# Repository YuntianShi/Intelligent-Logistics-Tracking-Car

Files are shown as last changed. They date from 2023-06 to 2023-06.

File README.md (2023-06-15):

# Intelligent-Logistics-Tracking-Car
This is a course design from Design &amp; Bulid Ⅰ(First Semester) and I am the leader of this project.  

<p align="center">
摘要
</p>  

&emsp;&emsp;智能机器人从诞生至今已经有了长足进步和发展。其中，能够自由移动对外界环境作出反应的智能循迹机器人更是其中的佼佼者，早已是智能机器人研究的重点领域。智能循迹机器人随着机械领域、计算机领域、微电子领域、自动化领域、传感领域等相关领域技术的不断发展突破而日俞完善，并逐渐广泛的应用于工业操作、宇宙探测、疫情管控、科研、军事和民用等方面。  

&emsp;&emsp;近年来，各大高校纷纷面向本科生开展智能机器人制作课程，立足于激发大学生的创新意识，培养学生的动手和团队协作能力。我校为培养新工科人才，为学生奠定良好的基础，设立了制作基于Arduino开发板的“智能派送车”项目。本文以“智能派送车”为研发对象，研究并设计了一种“塔”式投放的智能派送车，并进行了相应的商业可行性分析。  

&emsp;&emsp;首先，本项目研究了项目开发相应流程，确定了项目开发的日历和甘特图，对工作进行初步分解，进行组内团队分工，做出项目产品规划，确定了产品规格并进行了客户需求调研。  

&emsp;&emsp;其次，本文对研发对象进行了功能分解，确定产品整车结构-“塔”式结构，建立三维模型，绘制产品工程图，进行动画仿真，确定控制接线图，确定控制逻辑判断流程并写出相应代码。  

&emsp;&emsp;再次，确定零件毛胚规格，制作关键零件，购买外购件，经济预算控制，并完成整车组装、综合调试和优化相关工作。  

&emsp;&emsp;最后，在完成“智能派送车”制作的基础上，我们进行了项目开发经济分析、项目产品开发对社会的影响，确保了商业上的经济可行性。  

&emsp;&emsp;总之，本项目从现实入手，关注在全球疫情下的行业问题，结合商业经济分析，通过对机械、计算机、微电子、传感、自动化领域知识的运用，将创意转换为产品，在一组成员的共同努力之下，顺利完成了课程任务。  

&emsp;&emsp;接下来是一些项目图片展示：  

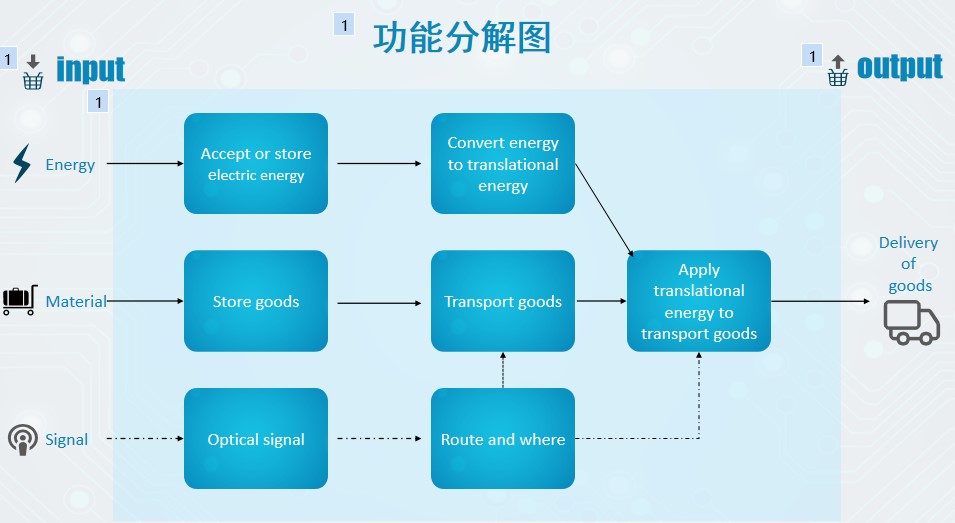
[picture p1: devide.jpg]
   

<p align="center">
图1 产品目标树
</p>  

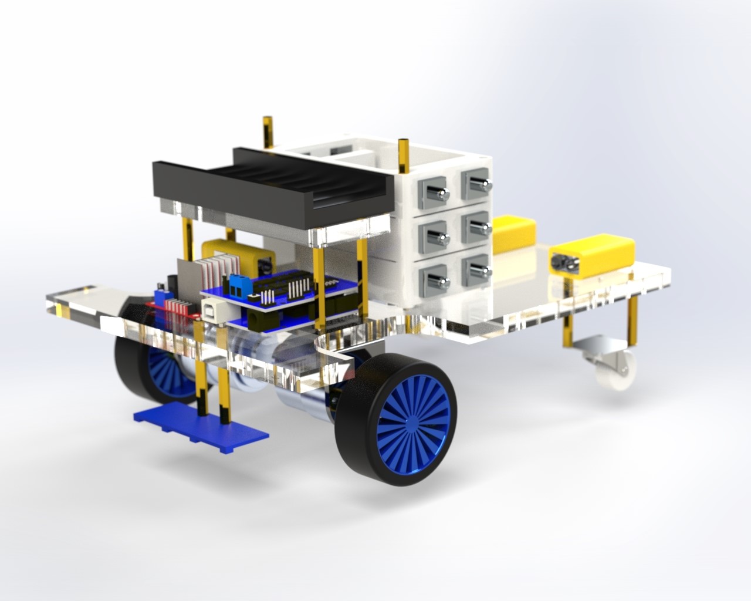
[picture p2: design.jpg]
  

<p align="center">
图2 整车设计图
</p>  

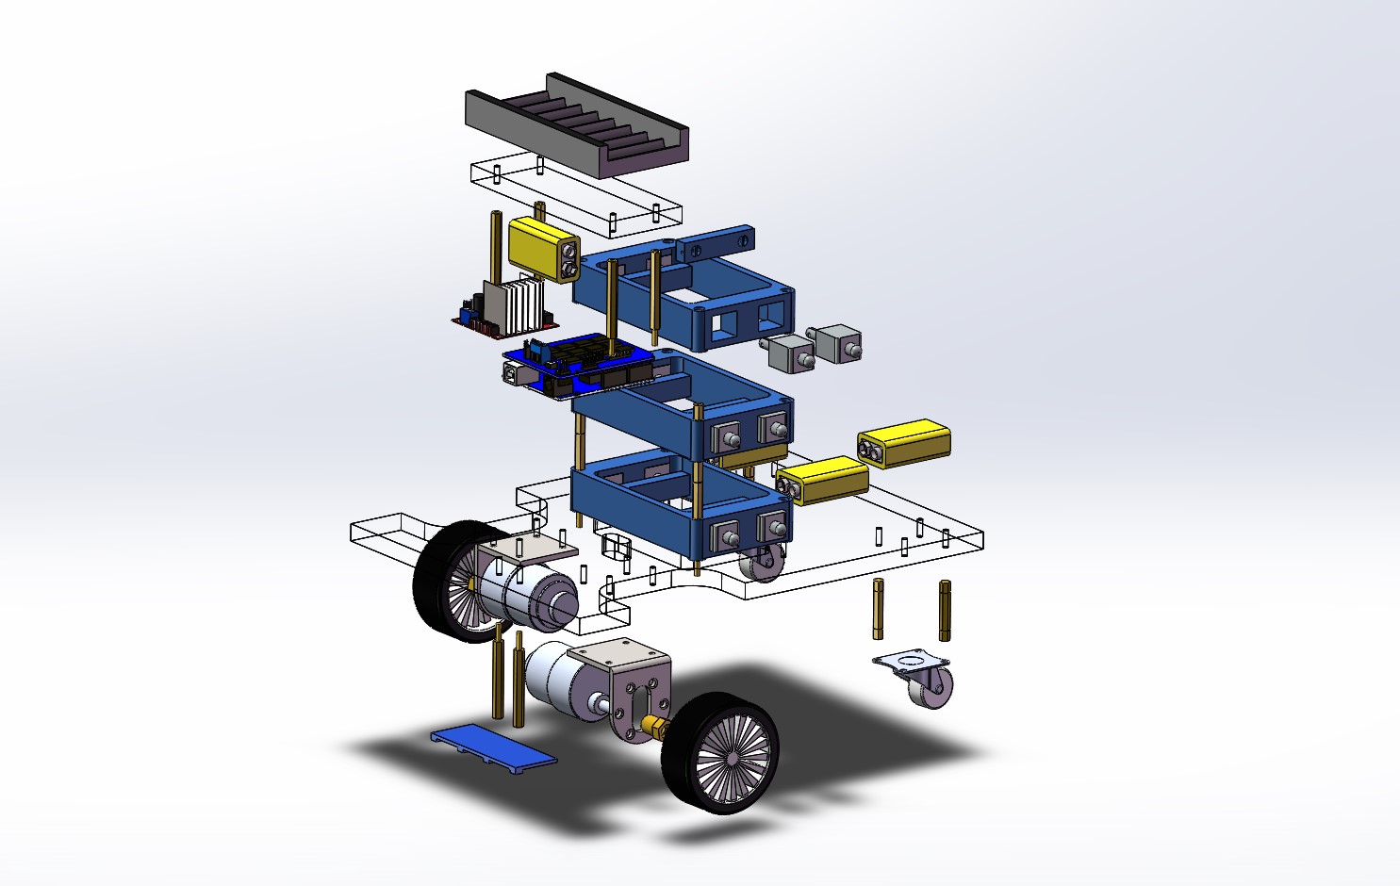
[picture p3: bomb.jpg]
   

<p align="center">
图3 整车爆炸图
</p>  

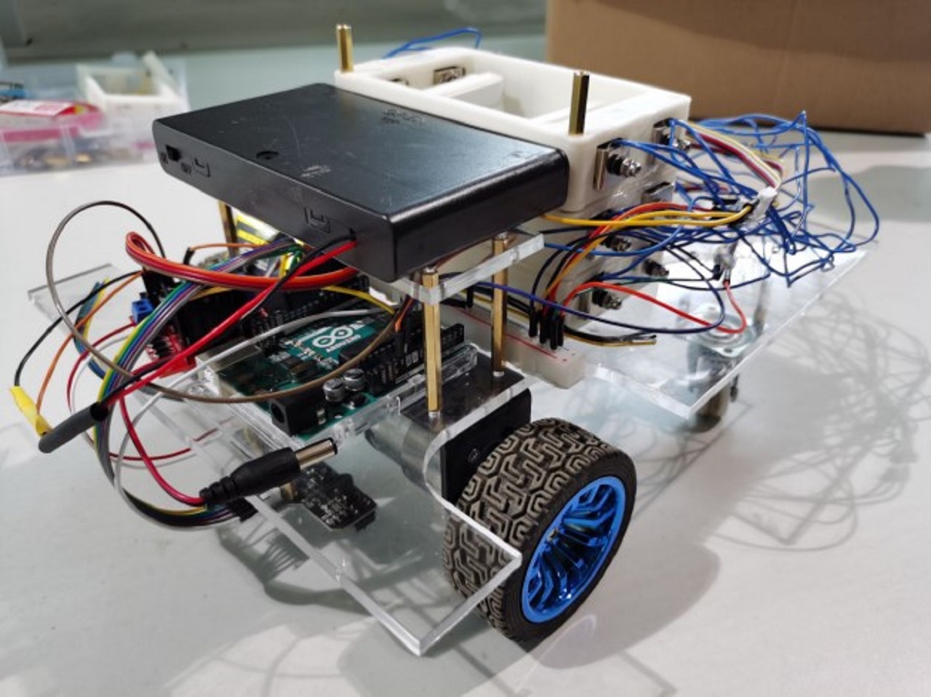
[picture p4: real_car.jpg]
  

<p align="center">
图4 实物演示图
</p>  

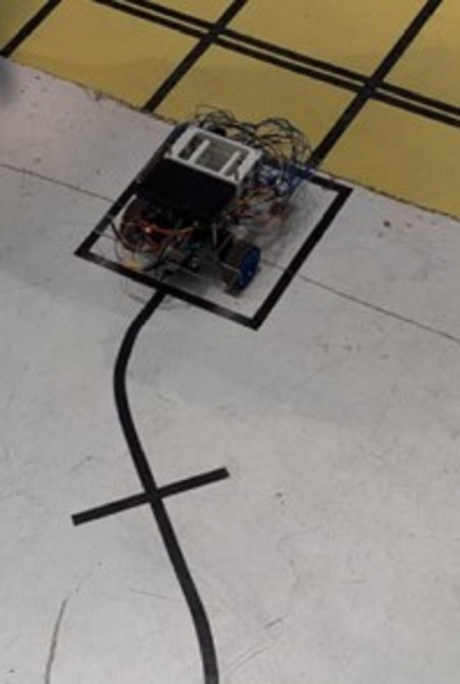
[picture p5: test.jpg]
   

<p align="center">
图5 实物测试图
</p>

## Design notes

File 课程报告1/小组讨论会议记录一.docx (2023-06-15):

设计与建造 课程小组会议记录

议题 | | 课程报告一
组长 | | 袁萌启 | 年级/班级/组别 | | | 2020级 2 班 第 1 组
组员 | | 石云天，马天翼，季若鱼，李贺航
会议时间 | 2020年9月30日 | | | 会议地点 | 46教A114
讨论内容 | 1.智能派送车的项目综述 2.团队组成分工与工作分解 3.团队接下来的计划以及团队日历和甘特图 4.工程师职责 5.对给课程所需知识进行初步的认识
下一步工作计划 | 进行产品规划，完成产品任务书以及产品任务调研，对客户需求进行分析，完成产品目标树，确定产品目标指标，产品规格参数，建立需求-指标矩阵。 对组内成员进行进一步了解，对组内分工进行调整和细化。
附件材料清单 | 《产品的设计和开发》，《Arduino程序设计基础》 《机械工程图学》

参会成员签字:袁萌启、马天翼、石云天、季若鱼、李贺航

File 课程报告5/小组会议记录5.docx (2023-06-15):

设计与建造 课程小组会议记录

议题 | | 课程报告五
组长 | | 袁萌启 | 年级/班级/组别 | | | 2020级 2 班 第 1 组
组员 | | 石云天，季若鱼，李贺航，马天翼
会议时间 | 2020.11.29 | | | 会议地点 | 郑东图书馆206读者研究厢
讨论内容 | 1. 对老师上课内容进行梳理。 2.对本次小组任务进行具体的分工。 3.整车装配并生成爆炸拆解，完成投放动画仿真。 4.设计控制系统并完成连线图。 5.绘制控制流程图并设计算法，完成代码。
下一步工作计划 | 1. 购置零件毛坯材料并确定尺寸规格。 2. 进行关键零件的制作并准备项目产品装配。 3. 准备实地测验并进行后期调试。
附件材料清单 | 《产品的设计和开发》 《Arduino程序设计基础》

参会成员签字：袁萌启，石云天，李贺航，马天翼，季若鱼

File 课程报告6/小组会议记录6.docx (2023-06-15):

设计与建造 课程小组会议记录

议题 | | 课程报告六
组长 | | 袁萌启 | 年级/班级/组别 | | | 2020级 2 班 第 1 组
组员 | | 石云天，季若鱼，李贺航，马天翼
会议时间 | 2020.12.10 | | | 会议地点 | 郑东图书馆206读者研究厢
讨论内容 | 1. 对老师上课内容进行梳理。 2.对本次小组任务进行具体的分工。 3.购置零件毛坯材料并确定尺寸规格。 4.进行关键零件的制作并准备项目产品装配。 5.准备实地测验并进行后期调试。
下一步工作计划 | 1. 对产品开发过程进行经济性分析，对成本进行把握。 2. 分析项目产品开发对社会的影响，做进一步的思考与准备。 3. 完成项目产品报告书，准备进行答辩。
附件材料清单 | 《产品的设计和开发》 《Arduino程序设计基础》

参会成员签字：袁萌启，石云天，李贺航，马天翼，季若鱼

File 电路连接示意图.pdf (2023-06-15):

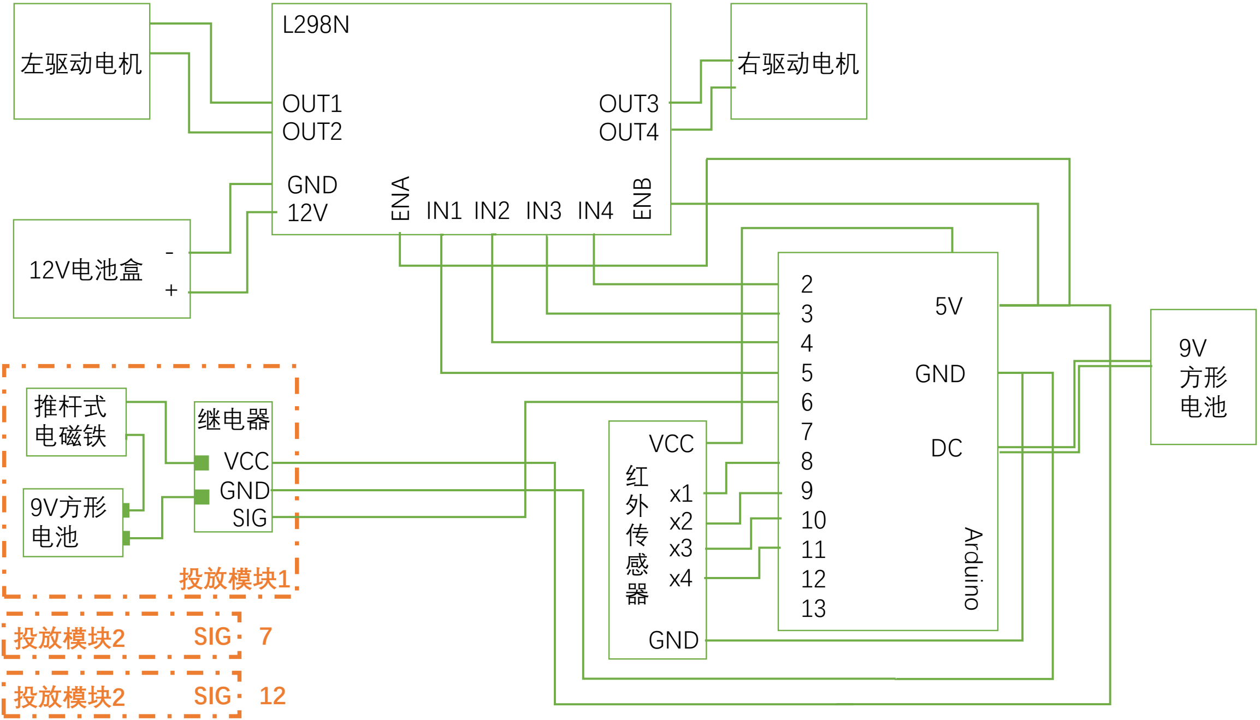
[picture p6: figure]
OUT1 OUT2; OUT3 OUT4; ENA; ENB; GND; 左驱动电机; 右驱动电机; 12V电池盒; 红外传感器; VCC; Arduino; 电池 继电器; VCC GND SIG 9V方形 电池; 推杆式 电磁铁; 投放模块; 2 SIG; SIG

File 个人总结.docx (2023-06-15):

石云天个人总结

进入大学的第一个学期，我接触到了一种以前从未接触过的教学方式——项目制教学，也第一次以小组的形式完成一整门课程。一个学期的时间眨眼间就过去了，设计与建造课程也要到了结课的时候，回顾这一个学期的课程，虽然十分辛苦，但在巨大的收获与最后成功带来的喜悦幸福面前，又显得不值一提。

首先，我想感谢为了这门课默默付出的每位老师、学长以及我最靠谱的队友们，没有每位老师的辛苦付出与耐心解答，我就没有机会体验到产品设计生产的整个工艺流程，没有机会收获这么多实用的知识与宝贵的实践机会。我的队友一直是我背后最坚实的后盾，我们在遇到困难时相互鼓励，在知识上互相交流、学习进步。这种相互促进、共同进步的氛围让我感到十分可贵，希望在日后其他的课程中也可以拥有这样的良师益友。

其次，我来陈述一下我在这个项目中为团队做出的贡献：制作课程报告一到六，完成报告书主体内容撰写，全程参与小车装配与程序调试；在整个学期的学习和探讨过程中：根据课程安排制作团队日历与项目安排甘特图；查阅并学习机电控制有关知识；根据客户需求调研结果完成产品目标树；学习并向组内同学讲述产品规划五步骤，协助完成产品任务书；学习并向组内同学讲述产品概念生成五步法，完成形态矩阵表与产品概念组合；完成驱动概念评分矩阵表；手绘小车草图；参与转向机构设计；建立项目产品三维模型；绘制项目产品2D图；绘制控制策略的逻辑判断流程图；制作投放机构投放动画仿真；参与代码编写；参加关键零件制作；参与整车装配与调试；确定零件毛坯材料与规格；学习相关知识并完成敏感性分析，绘制相关表格；完成小组会议记录七。通过这些任务的历练，我收获了许多。

最后，也是最重要的一个部分，我想说一下我的收获。

1、了解了整个设计生产的工艺流程。这门课设立的初衷就是让我们与实际的生产生活接轨，让我们了解现在实际生产中会应用哪些技术、使用哪些方法、在未来的实际工作中会面临怎样的情况，这也是天津大学“新工科”培养理念的最好体现。这门课从项目管理、产品规划、概念设计、详细设计、机电控制、代码调试、经济分析等多个方面由专业的老师系统地向我们介绍了相关的知识，然后以自己的智能投放小车作为实例，加以实践和运用。活学活用让我们的认识更加深刻、理解更加透彻。

2、极大的锻炼了我的沟通表达能力与团队协作能力。这门课创造性的开设了研讨课的形式，要求我们能够把自己的想法清楚明白的表达给别人，同时要符合任务规定的要求。我从最开始的不适应、不知所措到后来逐渐熟练、得心应手，是这门课的不断练习让我的表达能力得到提升，心理素质取得进步。这门课以小组方式进行，团队合作能力也是十分关键的，由于彼此之间不够熟悉，各自性格也不够了解，最开始的几次合作都陷入了僵局。但好在有组长的组织，他帮助我们破冰，化解尴尬气氛，经过几次的磨合，团队终于走上了正轨。我一直在反思之前我的问题，我有些过于内向，经常闷着不与同学交流，导致合作无法推进。从这之后，在每次小组会议上我都有意的增加我的发言，让队友可以及时了解我的意见与看法，最后的效果得到了明显的改进。这一学期的合作让我明白跟别人合作一定要足够主动，不要只是被动的听和接受，这样才能提高合作的效率，我相信这些收获在日后的学习和生活中一定会让我受益匪浅。

3、学会了很多软件的应用，激发了自学的热情与动力。设计与建造这门课有许多知识是需要我们在课下自学完成的，还有很多操作的实际演练是需要在课后完成的。这其中最有代表性的就是SOLIDWORKS的应用，最开始的时候只听了老师的讲解，课后自己操作时，只是一个小小的零件却花了我三个小时，当时我十分失望，甚至对自己的能力产生了怀疑。但正所谓“熟能生巧”，在队友的鼓励下，经过不断反复的练习，我可以比较熟练的操作了，真正掌握之后，我对这个软件产生了浓厚的兴趣，在课余时间会自己制作其他东西的3D模型，遇到不会的操作就去百度、去书上寻找解决的办法，在实践中探索学习，越学越有兴趣，既收获了技术，又收获了做完的快乐与成就感。通过这门课程我还掌握了arduino编程语言、fritzing软件绘制电路连线图、一部分机电控制的知识，在实践中探索，找到学习的兴趣与动力。

4、磨练了追求卓越、不轻言放弃的精神与魄力。整个过程中，耗时最久、最困难的部分就是最后的实地调试与代码优化。我们的小车最开始只能以三十多秒跑完整个赛道，并且投放也没有那么的精准。但正是我们对高品质的追求，驱使着我们不断改进，然而绝大多数的调整与测试都是以失败而告终的，我们的情绪逐渐都陷入了低谷。但是前面的困难有多大，最后成功的喜悦也会有多么的鼓舞人心。功夫不负有心人，在无数次的优化、测试后，我们的小车终于以不到15秒的时间跑完了全程，并且投放也比以前精准了许多。这次的经历教会了我永远不要满足于现状，一定要追求卓越，争取更上一层楼。我坚信这也会是我一生最为宝贵的财富。

这短短的一个学期，有苦有甜，既有前期耕耘受挫的压抑，也有最后顺利完成的激动。我会带着心中的这份感激，以更好的自己面对未来更多未知的挑战。

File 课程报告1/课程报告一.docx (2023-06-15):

课程报告1 项目计划

1.1 项目相关资料综述

项目综述：1、项目任务相关：本项目壹团队为单位，设计、建造并运行智能派送车，课程结束时各团队携带设计成果参加竞赛，完成研制报告和答辩。派送车从出发区发车，跟随地面轨迹线自主驶向终点。途中完成三个包裹的投放任务。2、智能派送小车：由智能派送车代替人工快递，减轻人工工作负担，提高工作效率，同时减少疫情期间人员流动。

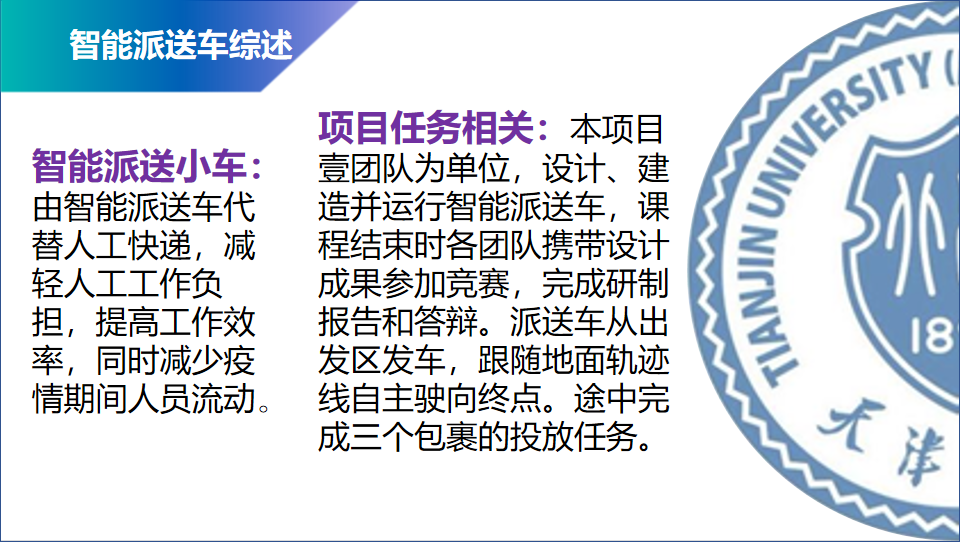
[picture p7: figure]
$[N360%(~$K[62R4L}Y)EOT

图1-1智能派送车综述

项目相关资料补充：1、工程：工程是利用科学原理来设计和建造机器，结构和其他项目，包括桥梁，隧道，道路，车辆和建筑物。工程学科包括广泛的更专业的工程领域；每个领域都更加侧重于应用数学，应用科学和应用类型的特定领域。2、工程设计：工程设计是一个系统化智能化的过程，在这个过程中，工程师为设备、系统或过程生成、评估和指定解决方案，这些设备、系统或过程的形式和功能在满足特定约束集的同时实现了客户的目标和用户的需求。换言之，工程设计是一个深思熟虑的过程，用于为设备、系统或过程生成计划或方案，这些设备、系统或过程在遵守特定约束的同时实现给定的目标。3、工程制图：工程图是生产中必不可少的技术文件，是在世界范围通用的“工程技术的语言”。正确规范的绘制和阅读工程图是一名工程技术人员必备的基本素质。制图的基本技能有尺规绘图、徒手绘图及计算机绘图。零件图、装配图的读图与绘制等。

4、机电一体化：机电一体化又称机械电子工程，是机械工程与自动化的一种，随着计算机技术的迅猛发展和广泛应用，机电一体化技术获得前所未有的发展。现在的机电一体化技术，是机械和微电子技术紧密集合的一门技术，他的发展使冷冰冰的机器有了人性化，智能化。5、机电一体化相关技术介绍：（1）精密机械技术(2)信息处理技术（3)检测与传感器技术（4)自动控制技术（5)伺服驱动技术（6）系统总体技术 6、Arduino: 构建于开放原始码simple I/O介面版，并且具有使用类似Java、C语言的Processing/Wiring开发环境。主要包含两个的部分：硬件部分是可以用来做电路连接的Arduino电路板；另外一个则是Arduino IDE，你的计算机中的程序开发环境。Arduino能通过各种各样的传感器来感知环境，通过控制灯光、马达和其他的装置来反馈、影响环境。板子上的微控制器可以通过Arduino的编程语言来编写程序，编译成二进制文件，烧录进微控制器。对Arduino的编程是通过 Arduino编程语言 (基于 Wiring)和Arduino开发环境(基于 Processing)来实现的。基于Arduino的项目，可以只包含Arduino，也可以包含Arduino和其他一些在PC上运行的软件，他们之间进行通信 (比如 Flash, Processing, MaxMSP)来实现。7、Arduino uno 简介：单片机： Arduino UNO控制器采用的是 Atmel 公司生产的ATmega328P-PU单片机。供电方式：1、USB接口通过USB 数据线,给UNO控制器提供5V的工作电压.2、通过5V引脚和GND供电,电压不大于5V。3、DC电源接口连接到UNO控制器上一个5V的稳压电路,给UNO控制器提供标准的5V工作电压。4、扩展引脚中的Vin引脚和DC电源接口一样。8、arduino平台特点：简单清晰、开放性、发展迅速。1.2 项目管理

团队组成：经过对有关知识的学习，我们了解了组成一个成熟的产品设计研发团队所需的分工大致如下：市场营销+设计（结构设计+电子设计）+制造+文案。同时结合我们小组成员的具体特长以及本着设计与建造课需要每位同学都学习到整个产品研发流程的宗旨，我们小组进行了如下的分工（每个人都会参与到整个智能小车设计开发的全过程，但分工有所侧重）：1、袁萌启：设置运输程序，设置循行路线，使小车能成功地完成任务，符合设计理念，达成初步设计，尽量满足市场调研所提出的市场需求。2、马天翼：主要负责快递小车的结构设计，需要规划快递装载与投放方案，设计小车行进方式，规划元器件布局，设计车体框架，使车体能构成完整系统，为任务提供硬件保障。3、石云天：负责利用机电一体化技术实现小车的运动停止，让小车有完整的驱动系统，同时利用arduino编程控制小车完成指定任务，实现智能化作业。4、季若鱼：负责完成课程报告书，ppt等文案的制作工作，并完成每位成员的任务完成情况小结以及小组的会议记录，和小组同学合作完成小车的制作。5、李贺航：对该方向智能机器人的发展历程进行调查，了解目前市场主流产品的优点及不足，确立该机器人研发过程中的方向。在后期产品制作的过程中负责对各零部件，主板等的绘图建模工作。

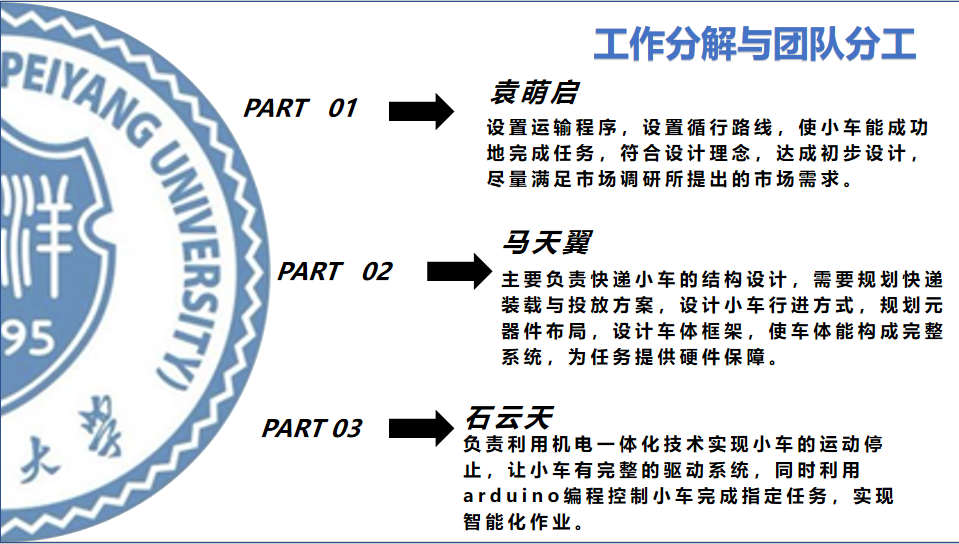
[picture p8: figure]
[VWECQA[2PA9Z1DA`LEHU)S
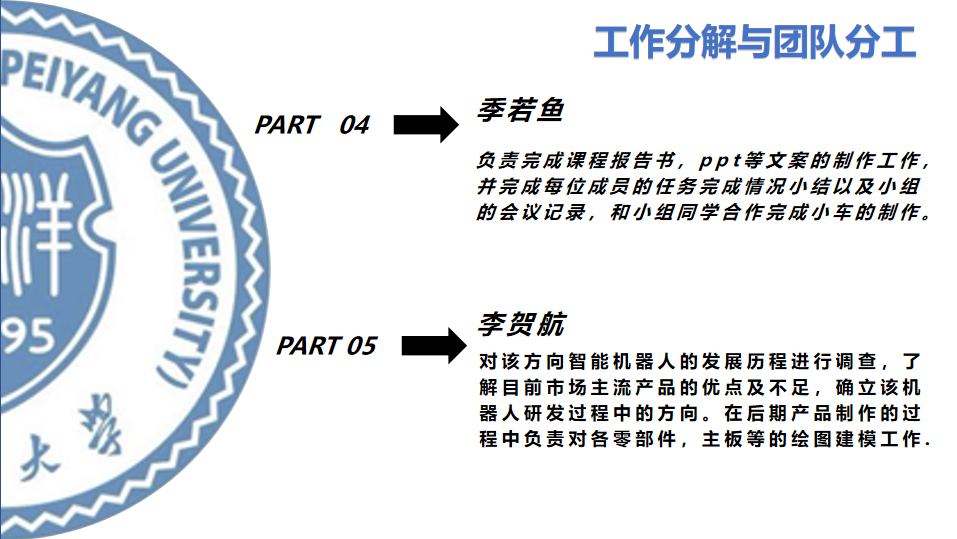
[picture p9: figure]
W{J(7H@X88TT$1}8Z5@2)G2

图1-2（a）团队组成与分工

图1-2（b）团队组成与分工

团队文化：有一个明确的挑战性的目标（智能配送车），从目标出发以结果构建团队结构，一群有才华有能力的团队成员，将团队需求放于个人需求之前的承诺，积极的团队文化（永不放弃，诚实守信，开创思维，相互尊重，民主开放），追求卓越的标准，从学部获得支持，团队有有效的领导。

工作分解：通过学习《产品的设计和开发》以及查阅产品研发的相关资料，我们小组把制造智能小车的项目进行了具体的工作分解，先是把它分成了八个子任务，而后又对子任务进行了更加细致的分解，利于我们以后更好的进行项目管理以及推动项目进展。

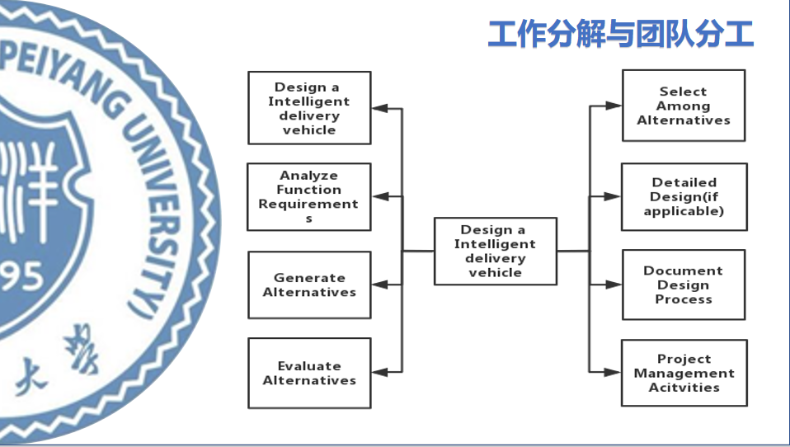
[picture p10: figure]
PR_UBB_3R%A}V}4[@(3(BZB
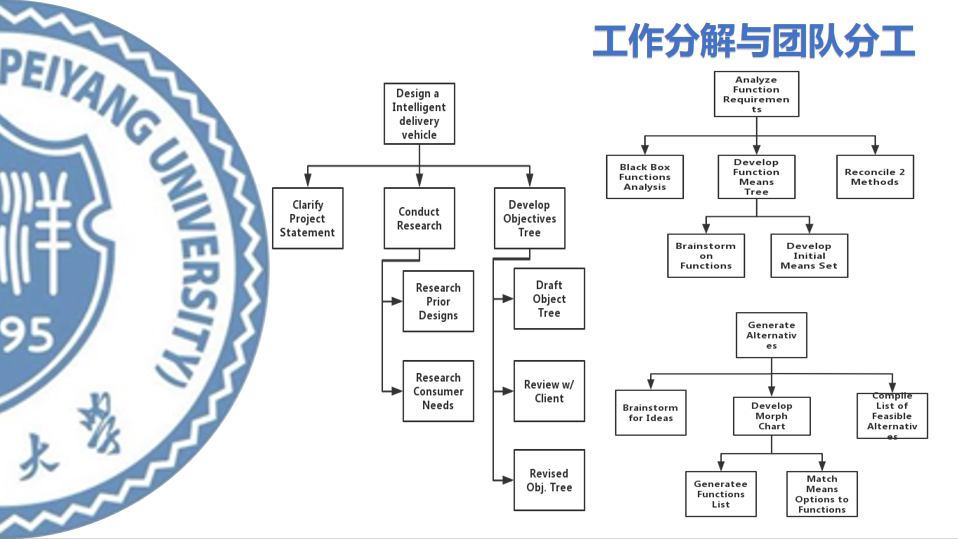
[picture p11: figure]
IGDXIKDPCQDB03Y5S)X9%EN

## 图1-2（c）工作分解

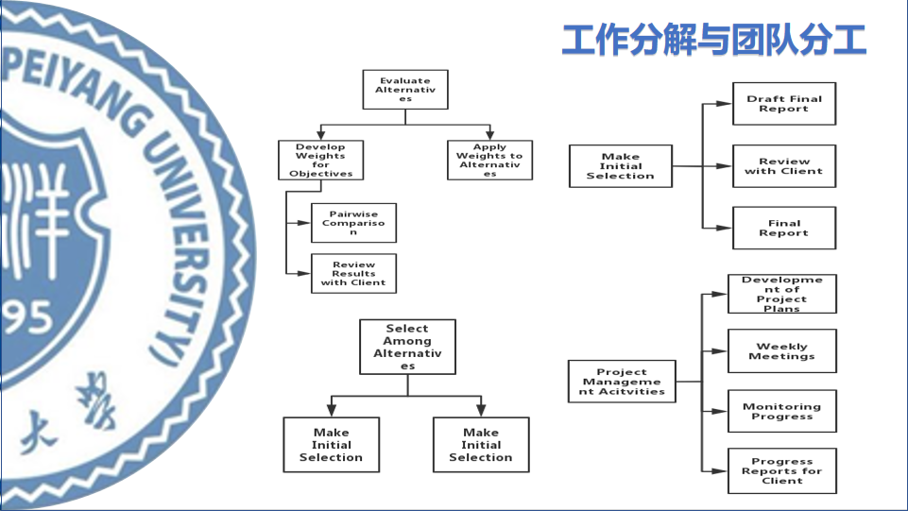
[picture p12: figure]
CK4FEP]}ZOXNFCRVPL(J4O0

## 图1-2（d）工作分解

图1-2（e）工作分解

团队日历：根据老师公布的课程安排以及自身的时间安排，我们制订出整个项目从开始阶段到最后成品制作完成的团队日历，让我们更加有计划的推动各个步骤的进展。

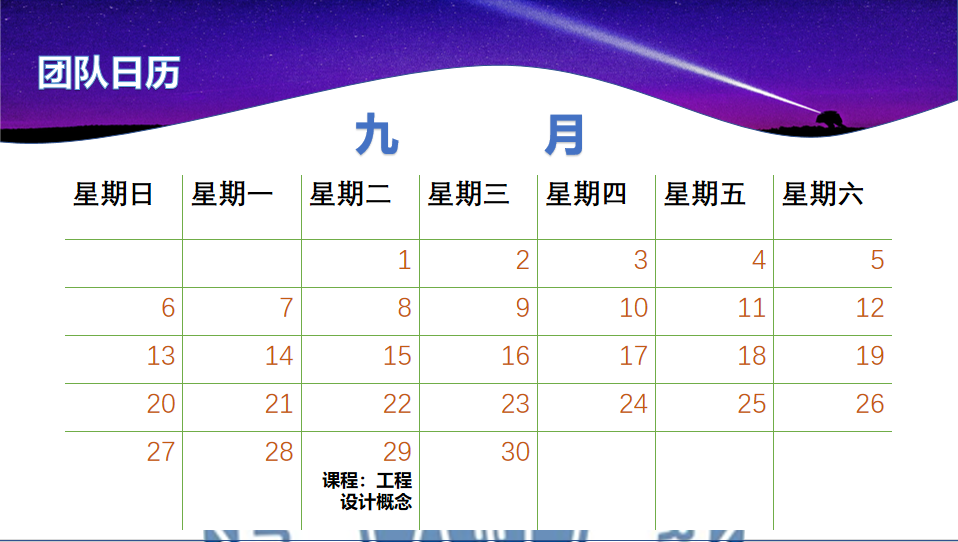
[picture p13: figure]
1]04S)S(92S3$]X]N0U{2ZV

图1-2（f）九月团队日历

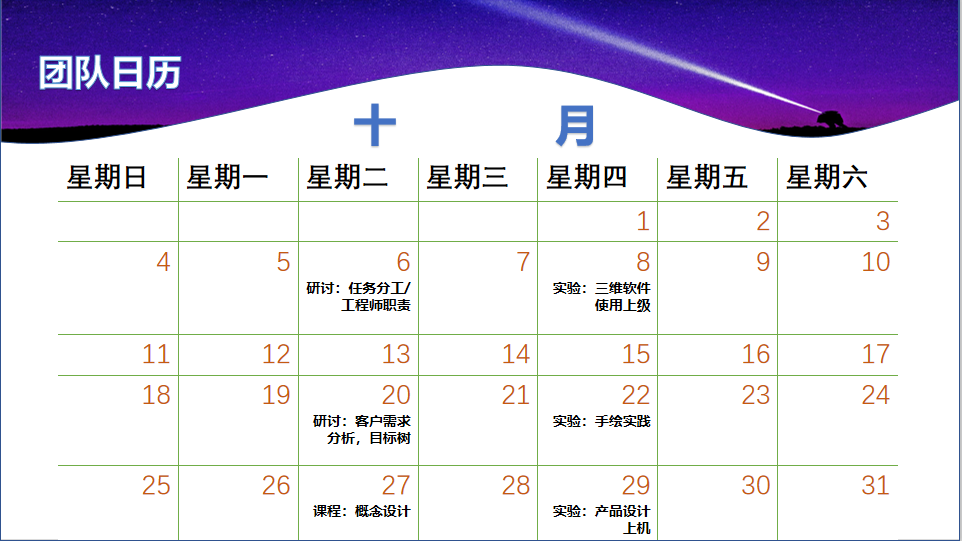
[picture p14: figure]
0`UL(A6_$}K$D)XN836]~{H
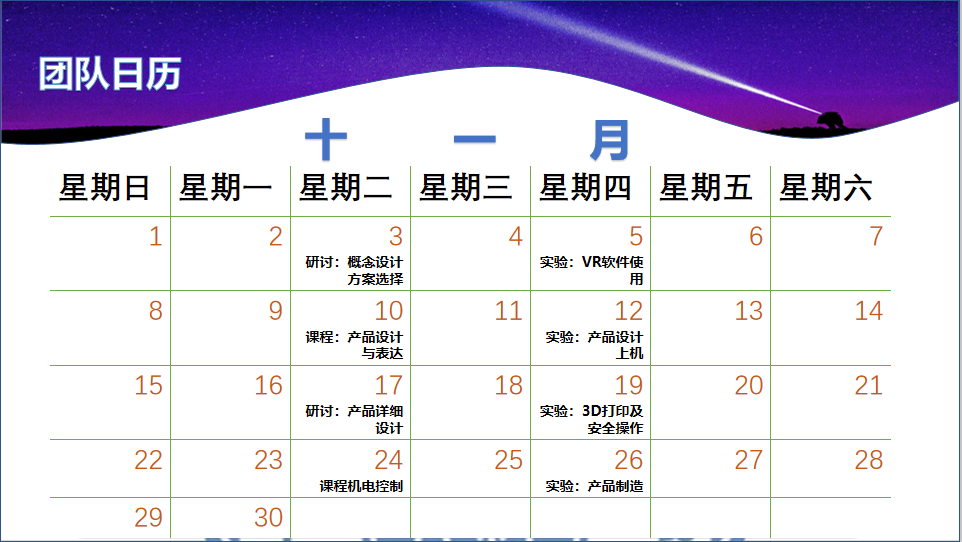
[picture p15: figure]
M439WEA8O3U]_G[_L~8`~H5

图1-2（g）十月团队日历

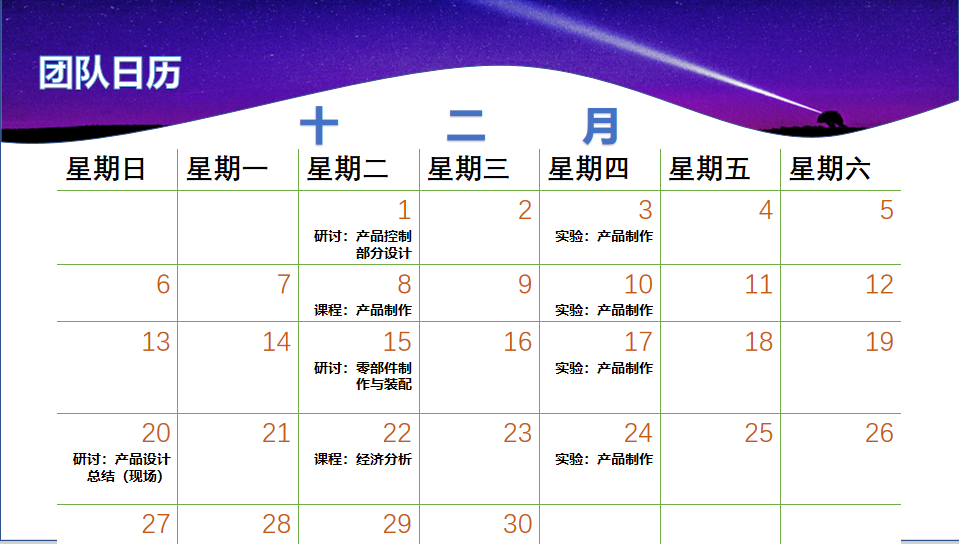
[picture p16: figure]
~~`G5LQ_0DK76NM0P16J@BV

## 图1-2（h）十一月团队日历

## 图1-2（i）十二月团队日历

项目安排甘特图：由于以前从未接触过这类图表，我们首先弄清楚了甘特图的具体含义（甘特图以图示通过活动列表和时间刻度表示出特定项目的顺序与持续时间。一条线条图，横轴 (https://baike.baidu.com/item/%E6%A8%AA%E8%BD%B4)表示时间，纵轴 (https://baike.baidu.com/item/%E7%BA%B5%E8%BD%B4)表示项目，线条表示期间计划和实际完成情况。直观表明计划何时进行，进展与要求的对比。便于管理者弄清项目的剩余任务，评估工作进度），然后了解了甘特图特点(甘特图的特点是突出了生产管理中最重要的因素— 时间，它的作用表现在三个方面：1、计划产量与计划时间的对应关系。2、每日的实际产量与预定计划产量的对比关系。3、一定时间内实际累计产量与同时期计划累计产量的对比关系),然后我们根据前面制作的团队日历以及工作分解与团队分工，制作出了我们小组的项目安排甘特图。

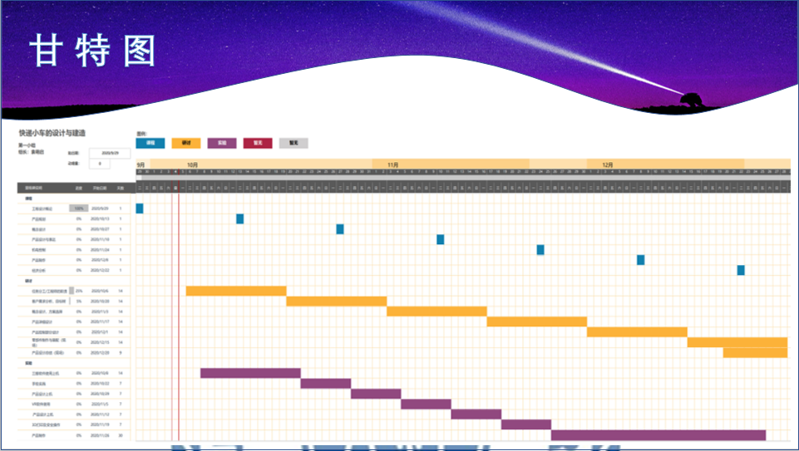
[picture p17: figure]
Q9IYP3@G9~)N_HIM9[NS2RQ

## 图1-2（j）项目安排甘特图

## 1.3 工程师职责

IEEE道德规范：1、承担与公众的安全、健康和福利相关的决策责任，及时披露可能危害公众或环境的因素。2、尽可能避免实在的或觉察的利益冲突，并在确实存在的情况下向受影响方披露。3、诚实并实际地基于现有数据索赔或评估。4、拒绝一切形式的贿赂。5、提高对技术的理解，合适的应用和潜在的后果。 6、保持和提高我们的技术能力，只有通过培训或经验的获得资格，或在充分披露相关限制后，才能为他人承担技术任务。7、寻求、接受和提出陈恳的技术工作批评，承认并纠正错误，正确评价他人的贡献。 8、公平对待所有人，不从事基于种族、宗教、性别、残疾、年龄、国籍、性取向、性别认同或性别表达的歧视行为。9、避免以虚假或恶意行为伤害他人及其财产、名誉或就业。10、协助同事和合作者的专业发展，并支持他们遵守这一道德准则。

工程师职责的自我认识：工程师则遵照一般性法则，从而在数学和科学上，解决了一些技术问题。有独立承担较复杂项目的研究、设计工作能力，能解决本专业范围内比较复杂的技术问题。较系统地掌握本专业的基础理论知识和专业技术知识，熟悉本专业国内外现状和发展趋势。有一定从事工程技术研究、设计工作的实践经验，能吸收、采用国内外先进技术，在提高研究、设计水平和经济效益方面取得一定成绩。对项目经理负责，负责软件项目的详细设计、编码和内部测试的组织实施，对小型软件项目兼任系统分析工作，完成分配项目的实施和技术支持工作。协助项目经理和相关人员同客户进行沟通，保持良好的客户关系。参与需求调研、项目可行性分析、技术可行性分析和需求分析。熟悉并熟练掌握交付软件部开发的软件项目的相关软件技术。负责向项目经理及时反馈软件开发中的情况，并根据实际情况提出改进建议。参与软件开发和维护过程中重大技术问题的解决，参与软件首次安装调试、数据割接、用户培训和项目推广。负责相关技术文档的拟订。负责对业务领域内的技术发展动态进行分析研究。

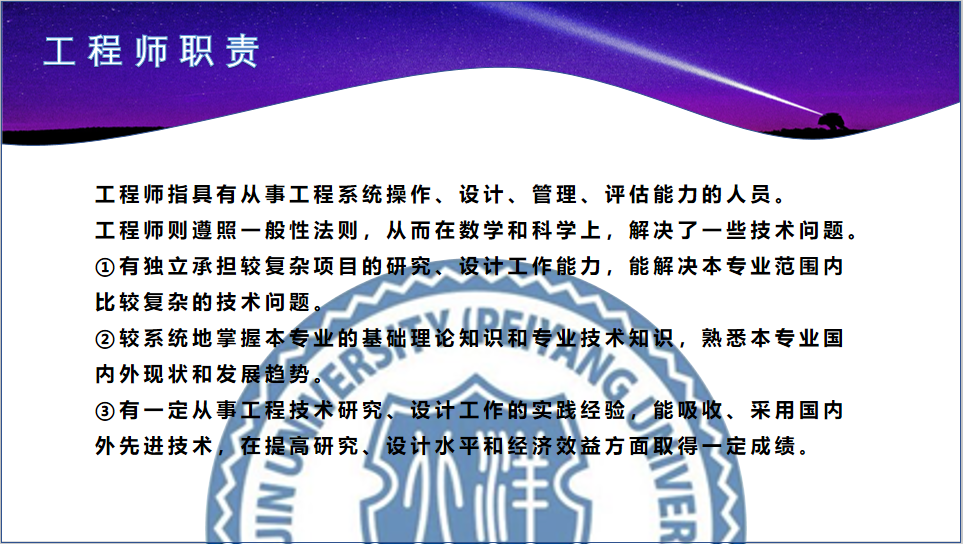
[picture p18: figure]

图1-3（a）工程师职责

1.4 任务完成情况小结

袁萌启：负责安排团队分工，建设属于本小组的团队文化；查阅项目有关资料；完成本次报告对应的ppt制作。

石云天：根据课程安排制作团队日历与项目安排甘特图；查阅并学习机电控制有关知识；制作并完善课程报告一。

马天翼：根据课程安排制作团队日历与项目安排甘特图；查阅并学习电路与编程有关知识；了解并向组内同学讲述工程师职责相关内容。

季若鱼:撰写项目综述，查找项目相关资料；查阅并学习三维建模有关知识，完成小组会议记录。

李贺航：学习并完成项目工作分解，制作工作分解流程图；查阅并学习结构设计有关知识。

1.5小组会议记录

设计与建造 课程小组会议记录

议题 | | 课程报告一
组长 | | 袁萌启 | 年级/班级/组别 | | | 2020级 2 班 第 1 组
组员 | | 石云天，马天翼，季若鱼，李贺航
会议时间 | 2020年9月30日 | | | 会议地点 | 46教A114
讨论内容 | 1.智能派送车的项目综述 2.团队组成分工与工作分解 3.团队接下来的计划以及团队日历和甘特图 4.工程师职责 5.对给课程所需知识进行初步的认识
下一步工作计划 | 进行产品规划，完成产品任务书以及产品任务调研，对客户需求进行分析，完成产品目标树，确定产品目标指标，产品规格参数，建立需求-指标矩阵。 对组内成员进行进一步了解，对组内分工进行调整和细化。
附件材料清单 | 《产品的设计和开发》，《Arduino程序设计基础》 《机械工程图学》

参会成员签字：袁萌启，石云天，李贺航，马天翼，季若鱼

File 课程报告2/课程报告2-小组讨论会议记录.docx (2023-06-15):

设计与建造 课程小组会议记录

议题 | | 课程报告二
组长 | | 袁萌启 | 年级/班级/组别 | | | 2020级 2 班 第 1 组
组员 | | 石云天，季若鱼，李贺航，马天翼
会议时间 | 2020.10.15 | | | 会议地点 | 郑东图书馆206读者研究室
讨论内容 | 1.对老师上课内容进行梳理。 2.对本次小组任务进行具体的分工。 3.对项目产品规划和产品任务书进行讨论. 4.对快递小车的客户需求和产品目标树进行调研和分析。 5.对产品的具体规格和参数以及需求-指标矩阵进行初步的设想和讨论。
下一步工作计划 | 1分析项目产品概念并绘制出形态矩阵表。 2每人手绘一份自己心目中小车的草图并在小组内部进行讨论。 3.完成对产品概念的初步组合以及对产品概念进行选择和评分。
附件材料清单 | 《产品的设计和开发》

参会成员签字：袁萌启，石云天，李贺航，马天翼，季若鱼

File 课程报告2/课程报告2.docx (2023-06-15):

课程报告2 项目产品规划

2.1 项目产品规划

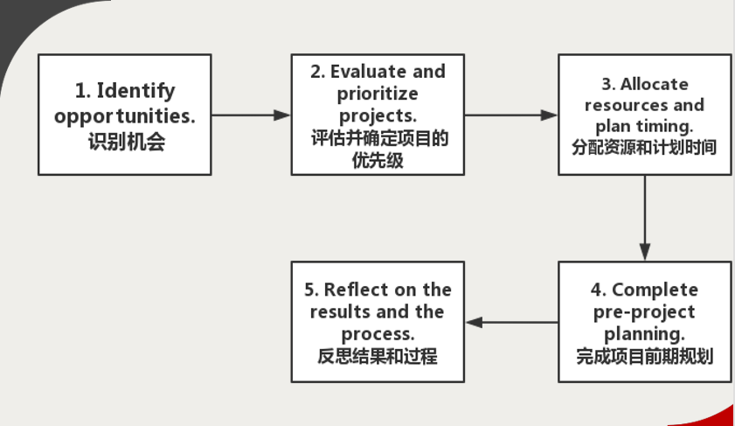
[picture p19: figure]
2UAYL68[J(]Y]]FSV4CYI8I

图2-1（a）产品规划五步骤

经过对上图产品规划五步骤的学习以及小组交流讨论，我们小组制订出智能快递小车产品规划五步法：

1.识别市场机会。规划流程诗语对产品开发机会的识别，这一步可以看成是机会漏斗，机会能可被动收集来的，但我们也会努力尝试去创造机会，并通过持续搜集各种构思，发现新产品机会。在我们的快递小车制作过程中，我们有着巨大的消费市场，伴随着快递小车的开发，我们也可以进行小车充电系统，小车维修系统的开发。

2.项目评价和优先级排序。需仔细讨论以下四个方面：竞争策略，市场细分，技术曲线和产品，平台讨论了这四个方面后，我们将讨论全新产品的机会评价，以及平衡项目的组合。在智能派送小车的市场调查中，我们发现市场对智能派送小车的速度以及工作时长的要求较高，需求较大，因此我们将把主要的技术突破和人力物力放在对小车的速度提升以及小车的充电装置的配置和电池容量的扩大。

3.资源分配和时间安排。需对每个项目每月，每季度，每年所需资源数量进行估计，迫使我们面对资源有限的事实，确定项目时间和顺序的方法，有时成为管道管理，需考虑产品上市时间，技术储备，市场准备，竞争等因素。我们的快递小车的上市时间是12月24日，我们将进行编程，机电，设计，绘图等方面的技术储备。

4.完成项目前期规划。这一过程涉及一个小的跨职能团队，称为核心团队。在此步骤中，我们需要完成小车的任务书，并假定条件和限制，完成人员配置和其他项目前期规划活动。我们的人员配置已经在报告一中展现，但较报告一有所改动，我们小组的所有成员都将进行所有任务，比如说机电，设计，绘图，编程的完成，只是不同任务的负责人不同。

5.对结果和过程进行反思。在反思过程中，我们发现我们的小组分工不合理，及时对分工进行了调整。

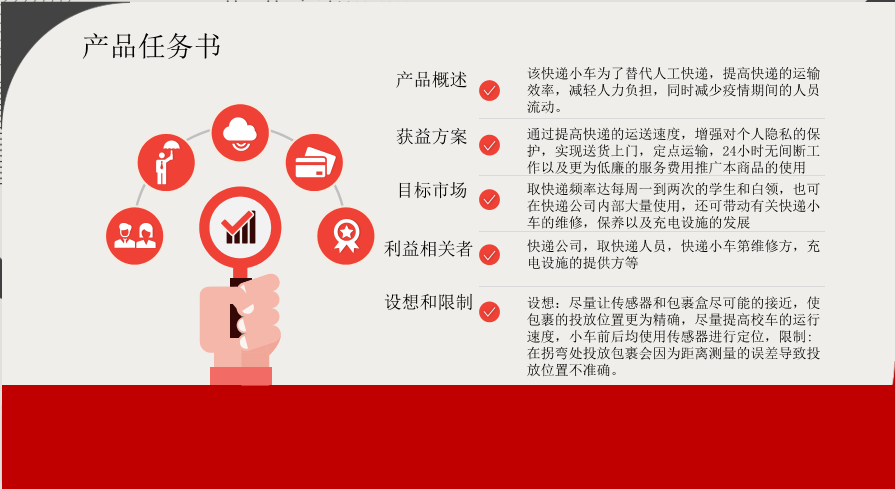
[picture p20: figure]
70G%U5NOY$FF4C){L%]KSGF

图2-1（b)产品任务书

产品任务书：该快递小车是为了替代人工快递，提高快递的运输效率和运输速度，减轻人力负担，同时减少疫情期间的人员流动。我们想通过提高快递的运送速度，增强的对个人隐私的保护，实现送货上门，定点运输，24小时无间断工作以及更为低廉的服务费推广本产品的使用，本产品有着广阔的目标市场，我们的重点目标市场是取快递频率达到每周一到两次的学生和白领，本产品也可以在快递公司内部大量使用，还可以带动有关快递小车的维修，保养以及充电设施的发展。

若该小车发展顺利，顺利上市，我们将会有快递公司，取快递人士，快递小车维修方，充电设施提供方等利益相关者。我们设想尽量让感应机构与包裹盒尽可能的接近，使包裹盒的投放位置更加精确，尽量提高小车的运行速度，小车前后最好都有感应机构，如果一切发展顺利，我们希望在一年后进行大规模的生产并投放市场，阿里巴巴公司建立资金链的联系，并争取在三年内获得一亿人民币的净利润。当然该小车也有他本身的制约，在拐弯处投放包裹会因为车辆距离的误差导致投放位置的不准确，以及因为速度的原因导致快递小车的底盘不稳。

2.2 客户需求调研

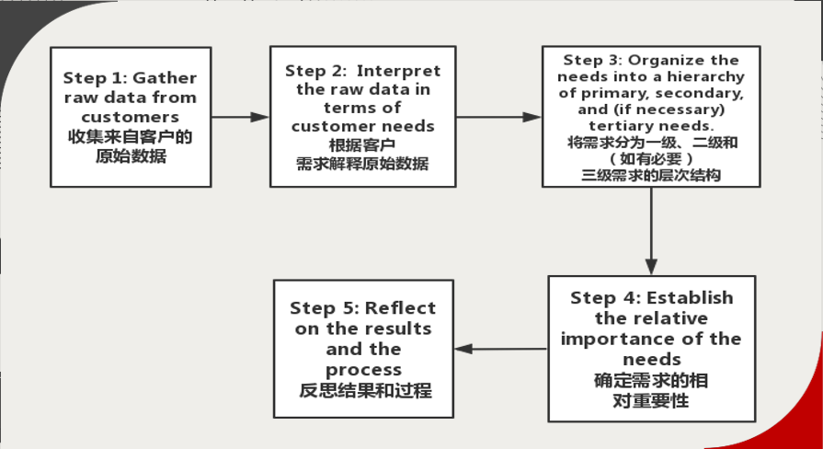
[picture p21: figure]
3}}F}F(%T67LOZ1]1%7L~GC

图2-2（a）客户需求调研五步骤

经过学习上面客户需求分析的五个步骤，我们小组经过商议制订出快递小车客户需求分析五步法：

1.从顾客那里通过访谈法，焦点小组。观察使用中的产品等方法收集原始数据。对顾客进行选择，清晰表达规格需求，归纳整理和顾客互动。我们进行了小车的问卷调查表，与客户进行互动，了解顾客需求。

2.从顾客需求角度理解原始数据。描述商品必须要用做什么而非怎么做，像原始数据一样尽量具体地表达需求，使用肯定句而非否定句，把需求表达成产品的一个属性，避免使用必须和应该。（此点在我们的ppt展示中已经有所体现）

3.组织需求的阶级。我们需求的阶级主要是经常取快递的白领和学生。

4.建立需求的相对重要性。在客户需求中，小车的速度和工作时间现代尤为重要，我们尽可能也要对小车的外形进行一定的修饰。

5.对结果和过程进行反思。我们进行了有关智能小车的问卷调查，调查的对象大多是23以下的学生，总共统计样本81份，以下是统计结果：

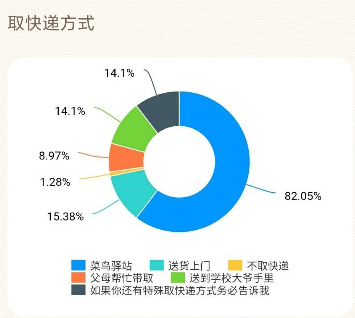
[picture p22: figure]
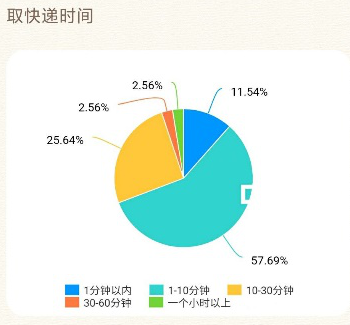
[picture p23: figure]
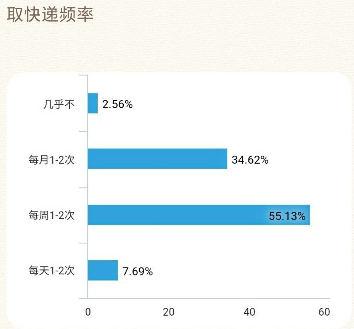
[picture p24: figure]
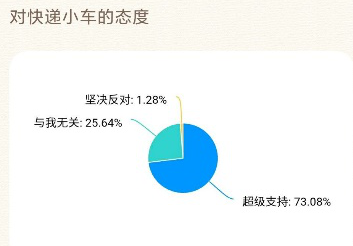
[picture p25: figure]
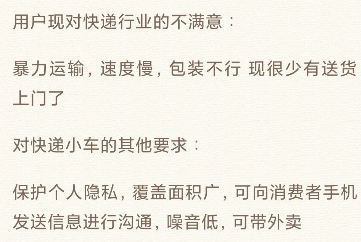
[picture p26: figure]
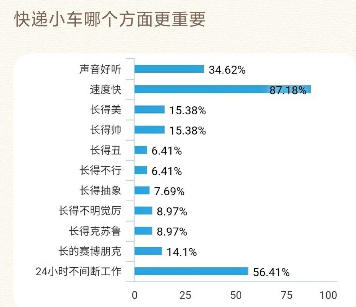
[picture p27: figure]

图2-2（b）用户调查统计图

由上可以看出客户希望取快递的时间控制在10分钟以内，工作时间尽量达到24小时无间断工作，实现送货上门，提高送快递的覆盖面积并提高快递的运送速度，提高快递包裹的完整程度，并有效保护客户的隐私。

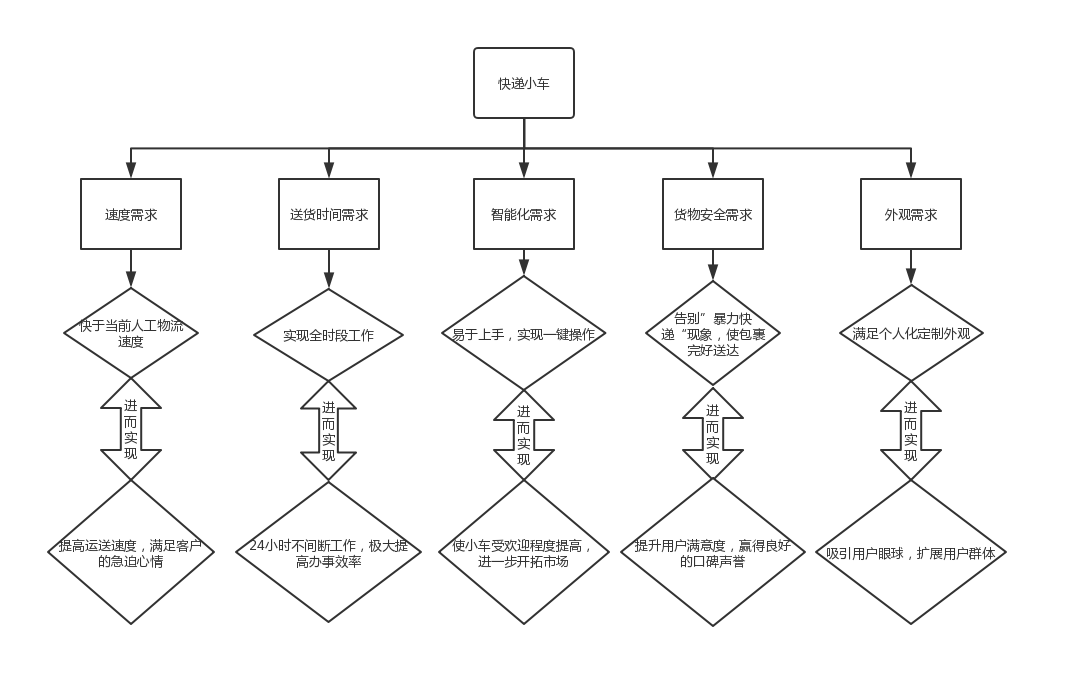
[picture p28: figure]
qt_temp

图2-2（c）智能快递小车产品目标树

基于客户需求调研得到的数据，我们绘制出了产品目标树。客户对于快递小车的需求总共分为“速度”“送货时间”“智能化”“货物安全”“外观”五个主要的部分。对于速度需求，人们的普遍要求是要快于当前的人工配送速度，以体现出机器人的优势，同时此举还可以提高客户的用户体验。在送货时间上，应当做到可以二十四小时无休息的配送，相对人工提高效率，但又需要注意，不能打扰用户的正常生活。小车智能化程度应当较高，易于新用户的上手与使用，尽量实现一键化操作，以提高小车的受欢迎程度，进一步开拓市场。快递当中最重要的便是货物的安全，一定要告别当前存在的“暴力快递”的现象，使包裹完好无损的送到用户的手中，为快递小车赢得良好的口碑和声誉。最后是外观方面的要求，我们会尽力实现个人化定制外观，以最大程度的满足客户的个人喜好，吸引用户的眼球，为我们开拓用户市场提供支持。

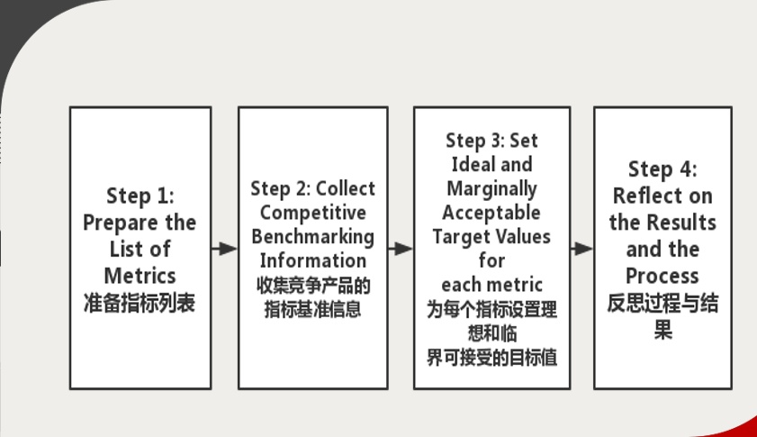
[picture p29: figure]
KJC(P_O7Y5MZWDJBU0_9@MM

2.3 产品规格

图2-3（a）产品目标指标建立四步骤

经过对上图产品目标指标建立四步骤的学习，我们制订出智能快递小车产品目标指标建立四步法：

1、 罗列出智能快递小车的各项重要指标，结合所给材料尺寸进行讨论。
2、 收集出竞争对手同类产品的指标基准信息，依据他们的漏洞与缺陷进行优化，使之更加符合用户使用需求，让我们的产品更具竞争力。
3、 根据第二步的结果为第一步罗列出的指标设置出理想与临界可接受的目标值。
4、 反思过程中出现的问题，为日后的工作提供经验参考。

经过智能快递小车产品目标指标建立的四个步骤，我们确定出智能快递小车初步的产品目标规格示意图，如下图：

图2-3（b)产品目标规格示意表

基于产品目标规格示意表，我们小组制订出了具体的产品规格参数表，确定了各个部件的大致位置以及车辆主体的大小尺寸，绘制出产品规格参数示意图，如下图所示：


图2-3（c）产品规格参数示意图1


图2-3（d）产品规格参数示意图2

图2-3（e）需求-指标矩阵

通过产品初步规划、客户需求分析以及制订出的产品规格参数，我们确定出智能快递小车的需求-指标矩阵，为我们下一步的工作提供参考、指明方向。

2.4 任务完成情况小结

袁萌启：制作问卷，收集并分析客户需求数据，完成客户需求调研；完成本次报告对应的ppt制作。

石云天：根据客户需求调研结果完成产品目标树；学习并向组内同学讲述产品规划五步骤，协助完成产品任务书；制作并完善课程报告二。

马天翼：学习并向组内同学讲述产品目标指标建立四步骤；确定小车具体参数，绘制产品参数示意图。

季若鱼:根据产品规划五步骤制作产品任务书；完成需求-指标矩阵；参与问卷制作；完成小组会议记录。

李贺航：学习并向组内同学讲述客户需求调研五步骤；制作问卷，收集并分析客户需求数据，完成客户需求调研。

2.5 小组会议记录

设计与建造 课程小组会议记录

议题 | | 课程报告二
组长 | | 袁萌启 | 年级/班级/组别 | | | 2020级 2 班 第 1 组
组员 | | 石云天，季若鱼，李贺航，马天翼
会议时间 | 2020.10.15 | | | 会议地点 | 郑东图书馆206读者研究室
讨论内容 | 1. 对老师上课内容进行梳理。 2.对本次小组任务进行具体的分工。 3.对项目产品规划和产品任务书进行讨论. 4.对快递小车的客户需求和产品目标树进行调研和分析。 5.对产品的具体规格和参数以及需求-指标矩阵进行初步的设想和讨论。
下一步工作计划 | 1分析项目产品概念并绘制出形态矩阵表。 2每人手绘一份自己心目中小车的草图并在小组内部进行讨论。 3.完成对产品概念的初步组合以及对产品概念进行选择和评分。
附件材料清单 | 《产品的设计和开发》

参会成员签字：袁萌启，石云天，李贺航，马天翼，季若鱼

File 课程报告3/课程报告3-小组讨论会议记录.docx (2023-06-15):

设计与建造 课程小组会议记录

议题 | | 课程报告三
组长 | | 袁萌启 | 年级/班级/组别 | | | 2020级 2 班 第 1 组
组员 | | 石云天，季若鱼，李贺航，马天翼
会议时间 | 2020.10.31 | | | 会议地点 | 腾讯会议
讨论内容 | 1. 对老师上课内容进行梳理。 2.对本次小组任务进行具体的分工。 3.对快递小车各个模块的产品概念进行讨论。 4.绘制出各个产品概念的草图，整合成为形态矩阵表，并且每位成员绘制出自己心目中小车的草图。 5.对产品的结构，原理，以及选择、评分标准进行初体设想和讨论。
下一步工作计划 | 1建立小车的3D模型，绘制产品的2D图，图标，尺寸标准。 2确定小车整体结构设计，标准件与配件使用。 3.确定小车转向机构，投放机构。 4.确定小车零件形状和尺寸，零部件之间的连接。
附件材料清单 | 《产品的设计和开发》

参会成员签字：袁萌启，石云天，李贺航，马天翼，季若鱼

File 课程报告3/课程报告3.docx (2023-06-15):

# 课程报告3 项目产品概念设计

## 3.1 项目产品功能分析

QQ图片20201125001542

图3-1（a）智能快递小车总体功能图

QQ图片20201125002342

快递小车的总体功能分为能量流、物质流和信号流三部分，通过智能小车的处理器使电能转化为运输物品的能量，把货物从快递点运送到客户手中，把传感器扫描到的亮暗信号转化为路径信息，实现循迹，从而实现小车的总体功能。

图3-1（b）智能快递小车细化功能分解图

快递小车在能量流上先把能量转化或储存为电能，再把能量转化为平动能。材料流上先储存货物，再运输货物，与能量流中的平动能共同应用于平动货物运输。信号流上先由传感器接收的光信号转化为路线和地点，为货物运输提供支持，最后与其他细化功能一起完成对货物的运输。

## 3.2 项目产品概念生成

QQ图片20201125005827

图3-2（a）概念生成五步法

进行项目产品概念生成需要经历五个步骤：1、澄清问题。要理解所生产产品的特性以及问题所在，并将问题进行分解，关注分解而成的子问题。2、外部搜寻。利用用户、专利、以及文献查找资料，标注重点并进行交流讨论。3、内部搜寻。从个人和集体两个层面进行商量讨论。4、系统性探索。制作分类树并加以组合生成组合表。5、反思结果和过程。反思整个概念生成的过程，提出建设性的建议与反馈。

我组首先将整个车辆的主问题分解为循迹、驱动、投放、刹车四个子问题，逐个进行解决。每人从网络上查找有关论文并从图书馆借阅图书查找资料，并记录出自己所认为的重点进行小组交流讨论。经过长时间的头脑风暴以及方案筛选淘汰掉一些难以实现的想法，每个模块产生出三到四种可行的概念与方案，加以相互组合，形成了组合表。最后回顾了整个的概念生成的环节，进行总结反思，发现了这个过程中存在的很多问题，获得了宝贵的经验同时了解了下次应格外注意的细节。

V@C[[FI]VO0@T)9}FW[7AN5

图3-2（b）形态矩阵表

之后我们小组对确定出来的每个模块中的各个概念进行了草图绘制，并加以汇总，得到了形态矩阵表。

产品概念组合

图3-2（c）产品概念组合

得出形态矩阵表后，小组成员对各个模块中的概念进行了合理地组合，得到了六种不同的产品概念组合，每种方案都有自己的优势与劣势，等待后续的打分评估。

马天翼

图3-2（d）马天翼手绘概念草图

石云天
袁萌启

图3-2（e）石云天手绘概念草图 图3-2（f）袁萌启手绘概念草图

季若鱼
李贺航

图3-2（g)季若鱼手绘概念草图 图3-2（h)李贺航手绘概念草图

在完成小车的产品概念组合后，每位小组成员对自己心目中小车的外观进行了绘制，得到了手绘概念草图。

## 3.3 项目产品概念选择

YW2%3JTZVAZ1D~LBZ3~CPYV

图3-3（a）概念选择六步法

进行概念选择主题上分为概念筛选和概念评分两个部分。概念筛选部分先是相对于共同的参考概念，进行快速粗略的评估，而后使用筛选矩阵进行具体的筛选。概念评分部分先细致的量化评估，后使用评分矩阵进行打分。综上可以汇总出概念选择的六步法：1. 准备选择矩阵 2. 产品概念评估 3. 产品概念排序 4. 对产品概念组合与改进 5. 选择一个或数个概念 6. 反思结果与过程。

9V~03MKP{(IUGZ~EB2[1MPS

图3-3（b）对产品模块概念的进一步选择

我们小组首先对形态矩阵表重点方案做出了进一步的选择。在循迹模块上我们初步选择了“色彩识别传感器”和“红外传感器”。在驱动模块上我们主体模式选择了两轮驱动，又细分为“前置前驱”和“前置后驱”两种。在投放模块中，我们暂时保留了全部的三种方案，他们具体的优劣势等待进一步的具体分析。在刹车模块中，我们排除了“鼓刹”这一概念，保留了“碟刹”、“盘刹”、以及“逆倒转刹车”三种方式。之后我们对各个模块以及3-2中提出的六种产品概念组合使用概念评分矩阵进行了细致的概念评分。

P4E6V{%QXQ)9E7%`)X5FKUJ

图3-3（c）循迹概念评分矩阵表

经过小组讨论，我们为循迹模块选择出了六项选择标准，并根据计算公式算出了每一项的权重，之后分别对三种概念进行了细致的评分，并依据权重计算出加权总分，再进行排序。最后得到总分最高、最具开发潜力的循迹概念是“红外传感器”。

6(KLH[9E7}VT06K}5`]G$R7

图3-3（d）驱动概念评分矩阵表

按照移动概念评分的模式，我们小组对驱动概念进行了评分排序，最后得到总分最高、最具开发潜力的驱动概念是“两驱：前置前驱”

投放打分

图3-3（e）投放概念评分矩阵表

经过小组讨论以及评分排序，总分最高、最具开发潜力的投放概念是“磁吸式（塔式）”

1JZ1%2XO[N1FU[(LH`{Z(1P

图3-3（f）刹车概念评分矩阵表

经过小组讨论以及评分排序，总分最高、最具开发潜力、可靠性最高的刹车概念是“逆倒转刹车”

总打分 (2)
总打分

图3-3（g）产品组合概念评分矩阵表

根据各个单项模块的评分筛选结果，我们小组对3-2中的六种产品组合概念进行了评分，绘制出产品组合概念评分矩阵表。我们首先依据课程报告2中的市场调研、客户需求分析以及应用时的关键指标制定出“速度”、“稳定性”、“投放精度”、“轨迹精度”、“成本”、“维修难易度”六项选择标准，并科学地为他们赋予了相应的权重。之后依照查阅到的资料背景以及单项打分比重对每种方案的六个指标进行了严格细致的评分，并计算出加权总分进行排序。经过了多重评分，最终我们为智能快递小车选择了认可程度最高、最可靠的“红外传感器+两驱：前置前驱+磁吸式（塔式）+逆倒转刹车”这一产品概念组合方案。

## 3.4 任务完成情况小结

## 袁萌启：完成刹车概念评分矩阵表、产品组合概念评分矩阵表；手绘小车草图；协助完成形态矩阵表；完成本次报告对应的ppt制作。

## 石云天：学习并向组内同学讲述产品概念生成五步法，完成形态矩阵表与产品概念组合；完成驱动概念评分矩阵表；手绘小车草图；制作并完善课程报告三。

## 马天翼：完成投放概念评分矩阵表、产品组合概念评分矩阵表；协助完成形态矩阵表；手绘小车草图。

## 季若鱼:学习并向组内同学讲述产品概念选择六步法，完成循迹概念评分矩阵表；协助完成形态矩阵表；手绘小车草图；完成小组会议记录。

李贺航：制作智能快递小车总体功能图与细化功能分解图；手绘小车草图。

## 3.5 小组会议记录

设计与建造 课程小组会议记录

议题 | | 课程报告三
组长 | | 袁萌启 | 年级/班级/组别 | | | 2020级 2 班 第 1 组
组员 | | 石云天，季若鱼，李贺航，马天翼
会议时间 | 2020.10.31 | | | 会议地点 | 腾讯会议
讨论内容 | 1. 对老师上课内容进行梳理。 2.对本次小组任务进行具体的分工。 3.对快递小车各个模块的产品概念进行讨论。 4.绘制出各个产品概念的草图，整合成为形态矩阵表，并且每位成员绘制出自己心目中小车的草图。 5.对产品的结构，原理，以及选择、评分标准进行初体设想和讨论。
下一步工作计划 | 1建立小车的3D模型，绘制产品的2D图，图标，尺寸标准。 2确定小车整体结构设计，标准件与配件使用。 3.确定小车转向机构，投放机构。 4.确定小车零件形状和尺寸，零部件之间的连接。
附件材料清单 | 《产品的设计和开发》

参会成员签字：袁萌启，石云天，李贺航，马天翼，季若鱼

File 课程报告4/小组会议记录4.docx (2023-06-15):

设计与建造 课程小组会议记录

议题 | | 课程报告四
组长 | | 袁萌启 | 年级/班级/组别 | | | 2020级 2 班 第 1 组
组员 | | 石云天，季若鱼，李贺航，马天翼
会议时间 | 2020.11.15 | | | 会议地点 | 腾讯会议
讨论内容 | 1.对老师上课内容进行梳理。 2.对本次小组任务进行具体的分工。 3.对快递小车的整车结构、转向机构、投放机构、零件的形状、尺寸与连接进行进一步讨论与确定。 4.绘制小车与零件的3D模型与二维工程图。
下一步工作计划 | 1.设计小车控制系统并完成连线图。 2.绘制控制流程图并设计具体算法加以实现。 3.确定零件毛坯的材料和规格，列出清单。 4.进行关键零件的制作。 5.整车装配并生成爆炸拆解，完成投放动画仿真。
附件材料清单 | 《产品的设计和开发》 《SOLIDWORKS2018从入门到精通》

参会成员签字：袁萌启，石云天，李贺航，马天翼，季若鱼

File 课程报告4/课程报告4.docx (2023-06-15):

课程报告四 项目产品详细设计

4.1 项目产品结构设计


图4-1（a）项目产品整车结构设计

项目产品整车结构设计：

在投放装置方面，我们考虑到传统的推杆式方案存在着物块易因受力不均匀而卡在通道中导致投放失败的问题，故设计了运用磁铁的“塔式磁吸夹”结构。

该方案中电磁铁通电后会对金属物块夹产生吸引作用，使物块两侧的夹子能在极短时间内同时收起，是物块能尽可能地保持稳定下落，防止其在通道内发生较大的翻滚而卡住；同时，两侧对称分布的夹子同时释放，也能使物块的受力尽可能地均匀且具有对称性，减少了物块在释放时发生不可预测的随机运动对系统的影响。同时，使用电磁铁相较于推杆式方案能减少复杂机械结构的使用，降低了系统因机械设计缺陷而发生故障的可能性，具体来说，即避开了推杆式系统中存在的“死点”问题。

“塔式磁吸夹”方案采用了模块化设计，即夹持单一物块的夹子都是统一规格的模块，使用时仅需将模块插入车身上的导轨即可，使得物块的载入更加方便，系统维护更加方便。

在车身设计中，还加入了“稳定架”结构，该结构用于将“塔式磁吸夹”的导轨顶端与车身相连，增强其稳定性，防止其结构因高度问题而发生水平方向上的晃动，增强了系统的稳定性。“稳定架”采用了易拆卸-装载设计，使得人员进行物块装载操作时能较为方便地拆卸和安装“稳定架”。

车底盘采用了不规则的形状设计，意在使车体重心尽可能降低，增加车体运动稳定性；同时，针对部件的安装做出的不规则设计使得车体更加紧凑，能尽可能缩小车身体积，增强其机动性。车身多处使用了圆角设计，减小车体被卡住的可能性，同时也进一步减小物块卡住的可能性。

车体在设计时预留了多余的空间，使车身尽可能拥有更大的适应能力与改装调整的空间。

标准件及自制件的选用：

在讨论过程中，我们小组结合自身需要和学部的条件，选取了驱动行驶轮电机车轮及其支架，电机驱动器，万向轮，传感器，电池盒，面包板，arduino开发板这些标准件，以及我们自己需要制作的车架，投放模块，稳定器的零件。

投放机构的设计：

在投放机构这一块，我们创新性的提出了磁吸式塔式结构这一方案。该方案中电磁铁通电后会对金属物块夹产生吸引作用，使物块两侧的夹子能在极短时间内同时收起，是物块能尽可能地保持稳定下落，防止其在通道内发生较大的翻滚而卡住；同时，两侧对称分布的夹子同时释放，也能使物块的受力尽可能地均匀且具有对称性，减少了物块在释放时发生不可预测的随机运动对系统的影响。

转向机构的设计：

在转向机构方面，我们小组选用了前置驱动差速转向的方案。后轮选用两个万向轮作为从动轮，在前轮的带动下实现整车的运动，通过对前轮两个轮子转速的差异控制，实现运动的转向。

标准件及自制件的形状与尺寸确定：


图4-1（b）行驶轮电机车轮极其支架

在提供的标准件中，驱动轮电机配套有轮胎和电机支架，我们根据标准件车轮的尺寸，确定了智能派送小车底盘高度30mm。


4-1（c）电机驱动器极其尺寸


4-1（c）万向轮及其尺寸


4-1（d）传感器极其尺寸


4-1(e)电池盒及其尺寸


4-1（f）面包板及其尺寸


4-1（g）arduino开发板

我们小组根据标准件的尺寸，确定了小车底盘的参数，并根据这些数据，运用solidworks构建了智能派送小车的3D模型。在智能派送小车各零件之间的连接上，我们尽可能的选用螺丝、螺栓进行连接，以保证既牢靠又便于拆卸。对于实在难以应用螺丝的连接处，我们选用502胶和透明胶带进行连接保证其稳固。

4.2 建立项目产品3D模型


4-2（a）车架的solidworks构型


4-2（b）投放机构的solidworks构型


4-2（c）稳定器的solidworks构型


4-2（d）智能派送车3D模型及其爆炸图

我们小组在确定好了零件使用及尺寸大小后，对各个标准件和自制件使用solidworks进行了构图，并对各个零件装配，完成了小车3D模型的构建。


4.3 绘制项目产品2D图

图4-3（a）车架2D图


图4-3（b）投放模块2D图


图4-3（c）稳定架2D图


图4-3（d）整车2D图

4.4 任务完成情况小结

## 袁萌启：参与项目产品整车结构设计和车身、车底盘结构设计；建立项目产品三维模型；绘制项目产品2D图；完成本次报告对应的ppt制作。

## 石云天：；参与转向机构设计；建立项目产品三维模型；绘制项目产品2D图；制作并完善课程报告四。

## 马天翼：参与项目产品整车结构设计和投放机构设计；设计建立项目产品三维模型；绘制项目产品2D图。

## 季若鱼:参与车身、车底盘结构设计；建立项目产品三维模型；绘制项目产品2D图；完成小组会议记录。

李贺航：确定标准件与自制件的选用，并确定其规格大小；建立项目产品三维模型；绘制项目产品2D图；。

4.5 小组会议记录

设计与建造 课程小组会议记录

议题 | | 课程报告四
组长 | | 袁萌启 | 年级/班级/组别 | | | 2020级 2 班 第 1 组
组员 | | 石云天，季若鱼，李贺航，马天翼
会议时间 | 2020.11.15 | | | 会议地点 | 腾讯会议
讨论内容 | 1.对老师上课内容进行梳理。 2.对本次小组任务进行具体的分工。 3.对快递小车的整车结构、转向机构、投放机构、零件的形状、尺寸与连接进行进一步讨论与确定。 4.绘制小车与零件的3D模型与二维工程图。
下一步工作计划 | 1.设计小车控制系统并完成连线图。 2.绘制控制流程图并设计具体算法加以实现。 3.确定零件毛坯的材料和规格，列出清单。 4.进行关键零件的制作。 5.整车装配并生成爆炸拆解，完成投放动画仿真。
附件材料清单 | 《产品的设计和开发》 《SOLIDWORKS2018从入门到精通》

参会成员签字：袁萌启，石云天，李贺航，马天翼，季若鱼

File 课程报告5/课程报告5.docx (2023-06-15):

# 课程报告5 项目产品控制部分设计

5.1 控制系统构成与连线图

控制系统构成：基于老师提供的器材以及小车自身控制需求，我们决定选用的控制元器件有：四路红外传感器、L298N、Arduino开发板。四路红外传感器是小车循迹的核心，是“小车的眼睛”它可以识别外界亮度，通过高低电频的变化来传递轨迹信号；Arduino是“小车的大脑”它控制着小车的一切运动，是小车循迹、投放的核心。L298N是我们比较陌生的控制元器件，我们首先查询了相关的资料，了解了它的用途与使用方法：L298N是步进电机驱动芯片。里面有两组H桥，使motor两端的电压维持在0~Vs之间（不考虑二极管的导通电压），防止motor两端电压过高或者过低，线上电压小于0时下端两个二极管跟地导通，大于VS时上端两个二极管跟VS导通，使电压维持在0~Vs之间，防止motor两端有过高的上冲或者过低的下冲。基于这些信息我们选择利用它来控制电机运动，进而使小车电机可以根据Arduino传输出的信号执行相应的指令，最终实现小车的转向与运动。

X(V6~R]{8VX$)AT72MV([F6

图5-1（a）控制元器件选用与控制系统构成构成

控制系统电路连线图：根据上述控制元器件的选择以及在书籍、网络中查找到的相关使用方法说明，我们绘制了控制系统的电路连线图以表明具体的连线方法，同时为后续的实物连线提供依据。


## 图5-1（b）控制系统电路连线图

## 整车装配与爆炸拆解：我们在以前的基础上重新构建出更加准确精细的整车装配模型并生成了爆炸拆解动画来进一步查看各个零件的位置与各零件间的连接关系。

B)`Q{U8`]_~J2{C%18Q~`K0

图5-1（c）小车爆炸拆解图1 图5-1（d）小车爆炸拆解图2


图5-1（e）小车爆炸拆解图3 图5-1（f）小车爆炸拆解图4

投放机构投放动作动画仿真：通过老师的指导与讲解，我们在原有的投放机构的基础上做了更加精细的设计，并制作了投放动作的动画仿真，让我们可以更加清晰的看到整个投放动作，对电磁投放机构工作方式有更加深刻的认识。

~RE[~NM3V~55CTGSK~OJJW3

图5-1（g）投放动作动画仿真示意图1 图5-1（h）投放动作动画仿真示意图2

## 5.2 控制流程图

在完成了控制系统元器件选择完成后，我们进入了具体的控制流程设计阶段。首先设计的是循迹系统的控制流程图，结合四路红外传感器的工作原理（检测为黑输出信号为0，检测为白输出信号为1），我们选择使用外侧的两路红外传感器，这样可以有一定的误差范围，使成功率变高，然后对具体会遇到的的转向运动情况进行了说明，具体见下图所示。其次是投放机构的的逻辑控制流程图，由于我们小组选择了三层塔式投放结构，我们在第一个投放点是底层的物块夹打开，进行第一次投放；到了第二个投放点，由于物块在中层，我们会把中层和底层的物块夹同时打开，以便物块正常掉落；到了第三个投放点，则是三层物块夹同时打开，使上层的物块掉落，完成整个投放过程。当小车行驶到最后一道黑线处，则会自动停车，结束整个循迹投放过程。

OO4B(0%7)KYJJ9RM5F{B(Z5

图5-2（a）控制策略的逻辑判断流程图

## 5.3 控制算法与实现

根据上一步绘制的控制策略的逻辑判断流程图，同时结合arduino语言的特点，我们进行了控制算法代码的编写，我们初步设定电机转速为110，同时到点停车投放，这个程序可以较好的完成小车所需的循迹与定点投放功能，达到项目所需要求：具体代码见附录1。


## 图5-3（a）代码实现示意图1


## 图5-3（b）代码实现示意图2


图5-3（c）代码实现示意图3


图5-3（d）代码实现示意图4

## 5.4 任务完成情况小结

## 袁萌启：参与控制元器件的选用，绘制控制系统连线图；参与代码编写；完成本次报告对应的ppt制作。

## 石云天：绘制控制策略的逻辑判断流程图；制作投放机构投放动画仿真；参与代码编写；制作并完善课程报告五。

## 马天翼：参与控制元器件的选用，绘制控制系统连线图；绘制控制策略的逻辑判断流程图；绘制智能投递小车爆炸拆解图；参与代码编写。

## 季若鱼:参与控制元器件的选用，绘制控制系统连线图；参与代码编写；完成小组会议记录。

李贺航：制作投放机构投放动画仿真；绘制智能投递小车爆炸拆解图。

## 5.5 小组会议记录

设计与建造 课程小组会议记录

议题 | | 课程报告五
组长 | | 袁萌启 | 年级/班级/组别 | | | 2020级 2 班 第 1 组
组员 | | 石云天，季若鱼，李贺航，马天翼
会议时间 | 2020.11.29 | | | 会议地点 | 郑东图书馆206读者研究厢
讨论内容 | 1. 对老师上课内容进行梳理。 2.对本次小组任务进行具体的分工。 3.整车装配并生成爆炸拆解，完成投放动画仿真。 4.设计控制系统并完成连线图。 5.绘制控制流程图并设计算法，完成代码。
下一步工作计划 | 1. 购置零件毛坯材料并确定尺寸规格。 2. 进行关键零件的制作并准备项目产品装配。 3. 准备实地测验并进行后期调试。
附件材料清单 | 《产品的设计和开发》 《Arduino程序设计基础》

参会成员签字：袁萌启，石云天，李贺航，马天翼，季若鱼

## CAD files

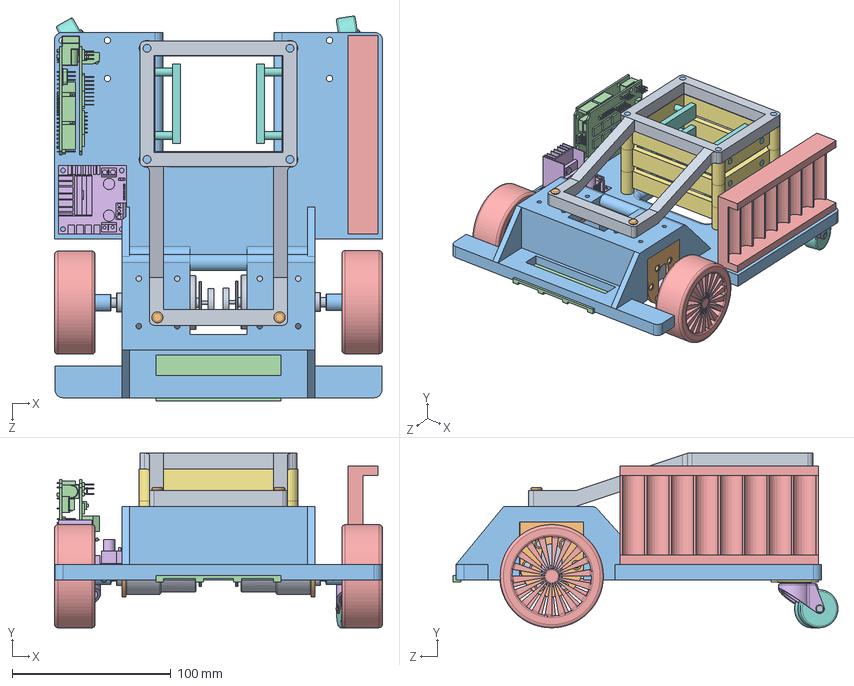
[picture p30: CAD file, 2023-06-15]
Solidworks模型/装配体1.SLDASM
206.9 x 110.0 x 242.6 mm
行驶轮电机 x 2
行驶轮电机支架 x 2
电机轴联轴器 x 2
传感器
车轮 x 2
连接 x 2
万向轮基座 x 2
万向轮轮子 x 2
轴1 x 2
轴2 x 2
ArduinoUNO扩展板
电池盒
电机驱动器
框架 x 3
夹子 x 6
稳定架
螺栓 x 2

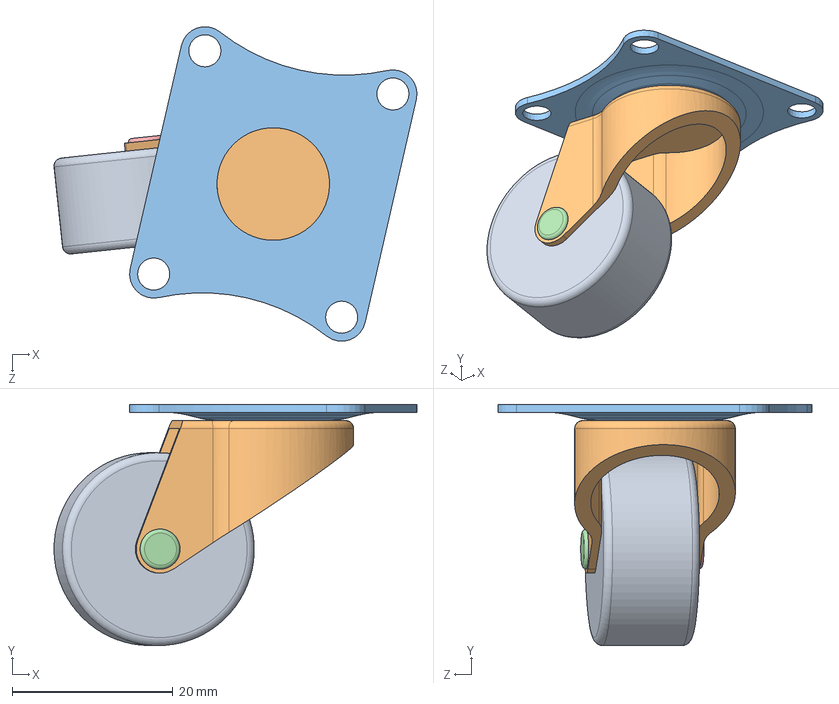
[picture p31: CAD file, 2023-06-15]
Solidworks模型/备用/装配体.SLDASM
45.2 x 30.0 x 39.1 mm
万向轮轮子
连接
万向轮基座
轴1
轴2

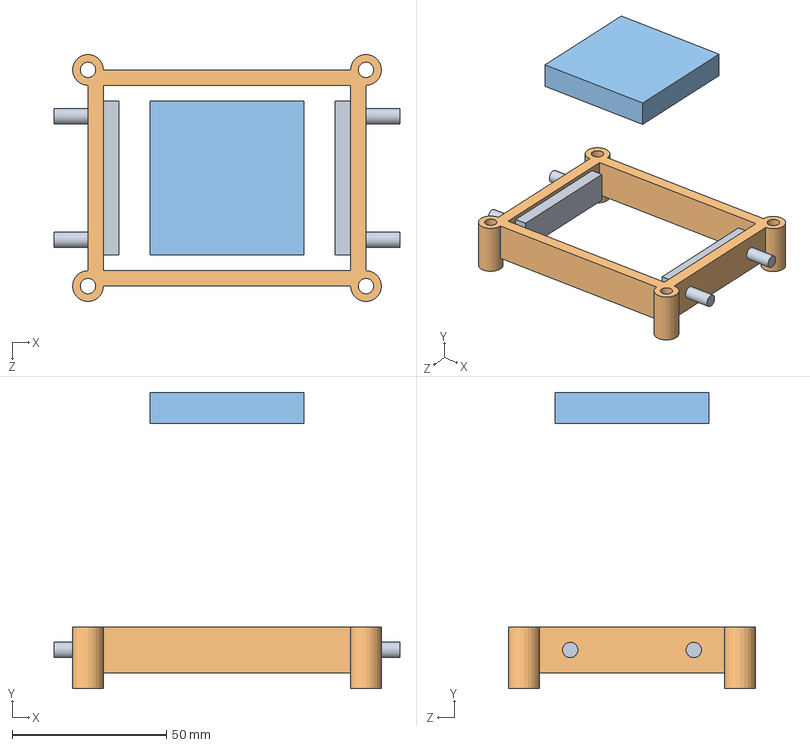
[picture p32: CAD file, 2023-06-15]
Solidworks模型/投放模块/投放模块装配体.SLDASM
112.0 x 95.9 x 80.0 mm
夹子 x 2
框架
物块

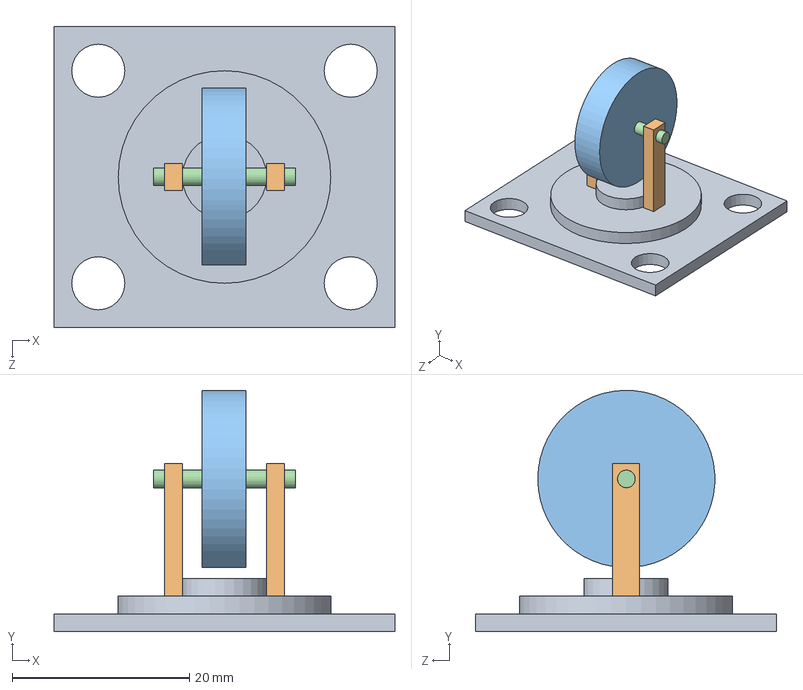
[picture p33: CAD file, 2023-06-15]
Solidworks模型/万向轮＆传感器/装配体万向轮.SLDASM
38.5 x 27.2 x 34.0 mm
万向轮
支架 x 2
轮子
横轴

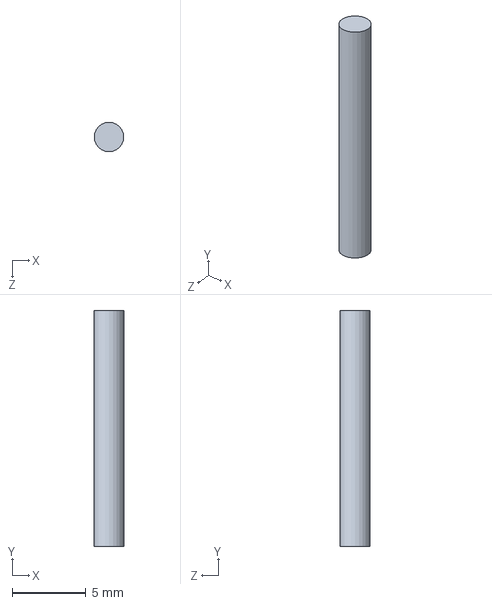
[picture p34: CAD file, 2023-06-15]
Solidworks模型/万向轮＆传感器/横轴.SLDPRT
2.00 x 16.0 x 2.00 mm

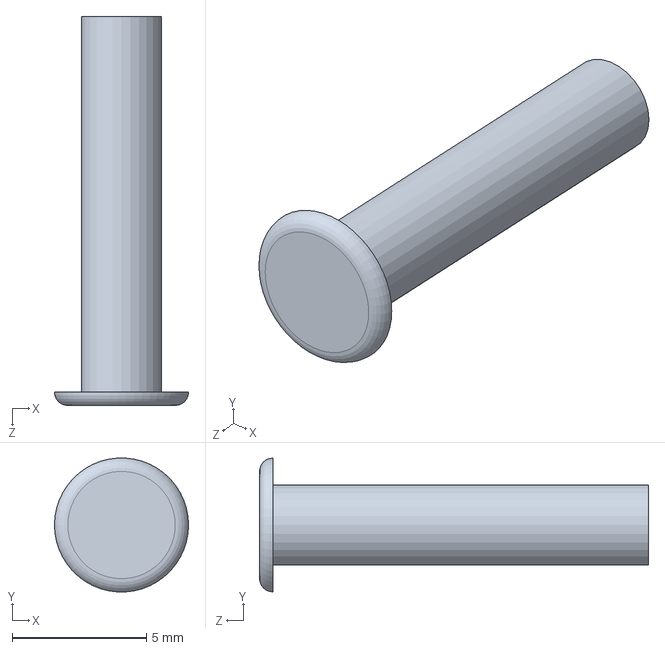
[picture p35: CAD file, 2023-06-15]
Solidworks模型/备用/轴2.SLDPRT
5.00 x 4.99 x 14.5 mm

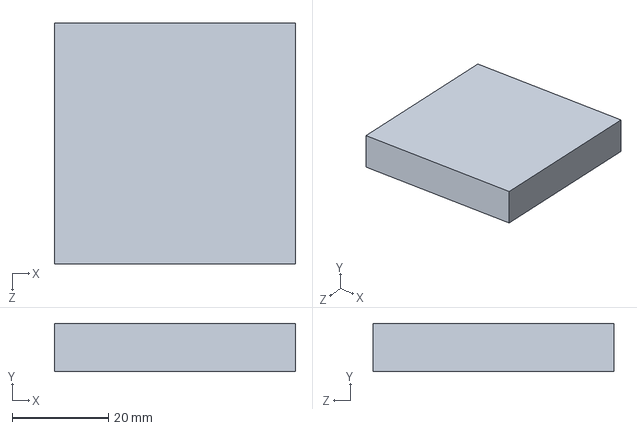
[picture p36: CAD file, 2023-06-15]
Solidworks模型/投放模块/物块.SLDPRT
50.0 x 10.0 x 50.0 mm

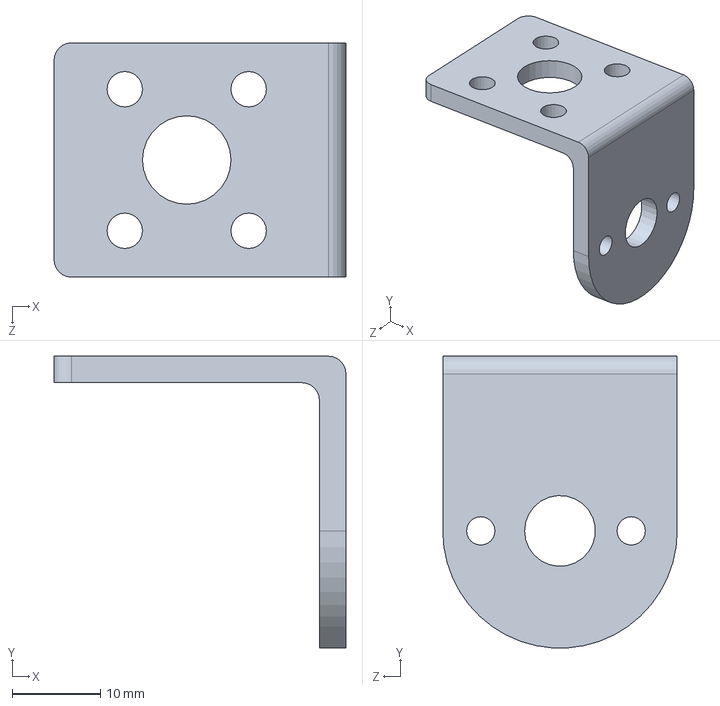
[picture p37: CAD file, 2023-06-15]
Solidworks模型/电机/投放机构电机支架.SLDPRT
33.0 x 33.0 x 26.5 mm

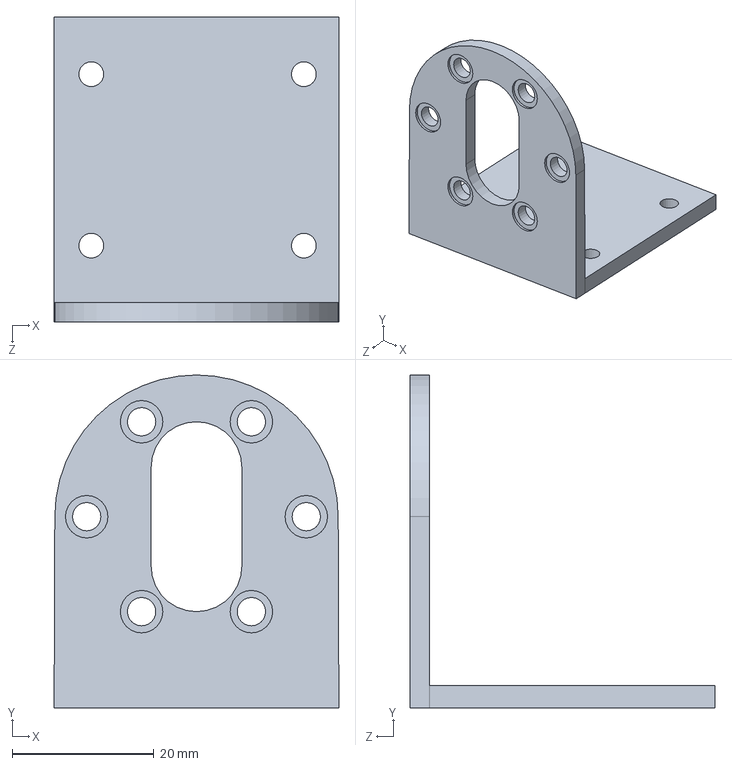
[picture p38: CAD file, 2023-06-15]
Solidworks模型/电机支架＆电机驱动器/行驶轮电机支架.SLDPRT
40.2 x 47.0 x 43.0 mm

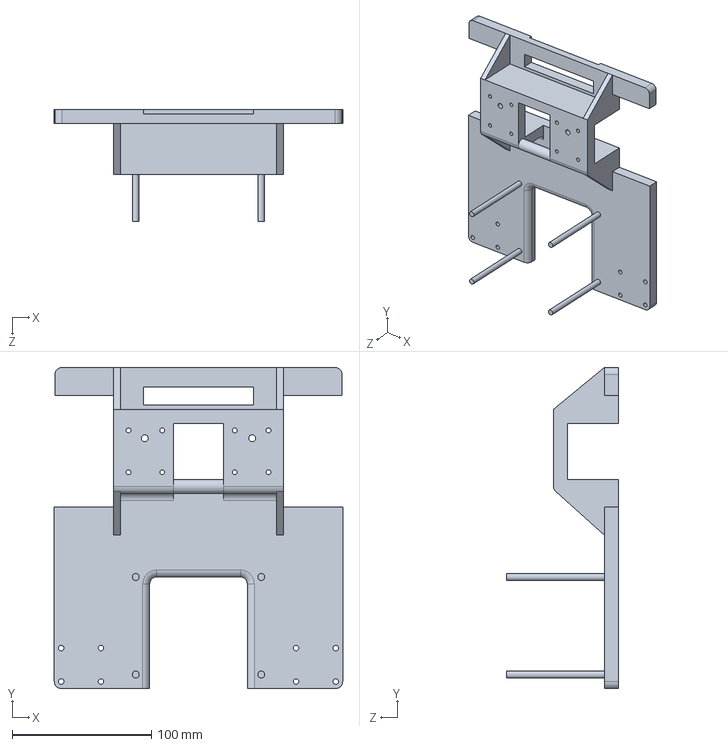
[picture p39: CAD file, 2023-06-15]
Solidworks模型/车架/车架.SLDPRT
206.9 x 230.2 x 80.0 mm

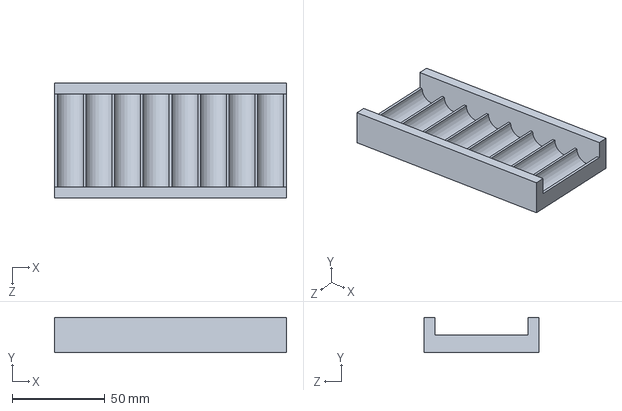
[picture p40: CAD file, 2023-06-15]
Solidworks模型/车轮/电池盒.SLDPRT
125.0 x 19.0 x 62.0 mm

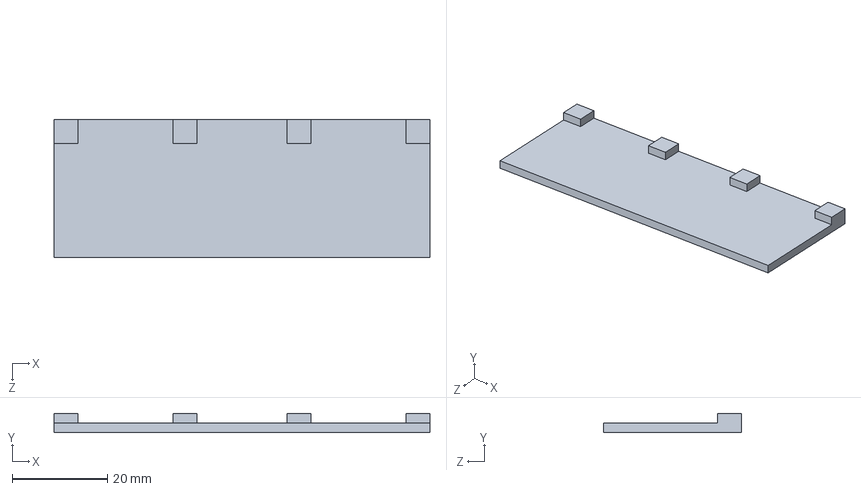
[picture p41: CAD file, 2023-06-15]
Solidworks模型/万向轮＆传感器/传感器.SLDPRT
79.0 x 4.00 x 29.0 mm

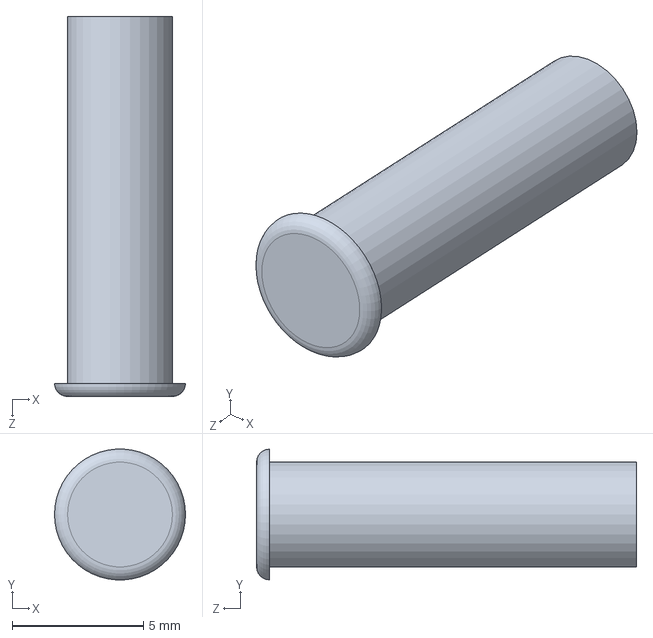
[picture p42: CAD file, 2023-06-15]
Solidworks模型/备用/轴1.SLDPRT
5.00 x 4.99 x 14.5 mm

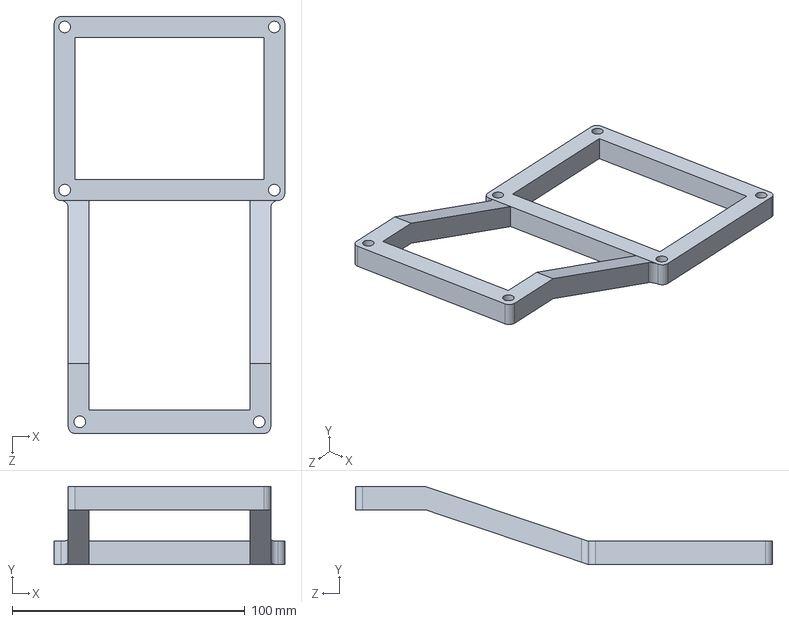
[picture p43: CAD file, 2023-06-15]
Solidworks模型/投放模块/稳定架.SLDPRT
99.0 x 33.5 x 179.0 mm

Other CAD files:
Solidworks模型/电机/电机轴联轴器.SLDPRT
Solidworks模型/电机支架＆电机驱动器/电机驱动器.SLDPRT
Solidworks模型/车轮/车轮2.SLDPRT
Solidworks模型/万向轮＆传感器/轮子.SLDPRT
Solidworks模型/万向轮＆传感器/万向轮.SLDPRT
Solidworks模型/万向轮＆传感器/万向轮工程图.SLDDRW
Solidworks模型/万向轮＆传感器/传感器工程图.SLDDRW
Solidworks模型/万向轮＆传感器/支架.SLDPRT
Solidworks模型/万向轮＆传感器/支架工程图.SLDDRW
Solidworks模型/万向轮＆传感器/横轴工程图.SLDDRW
Solidworks模型/万向轮＆传感器/装配体万向轮工程图.SLDDRW
Solidworks模型/万向轮＆传感器/轮子工程图.SLDDRW
Solidworks模型/备用/万向轮基座.SLDPRT
Solidworks模型/备用/万向轮基座工程图.SLDDRW
Solidworks模型/备用/万向轮轮子.SLDPRT
Solidworks模型/备用/万向轮轮子工程图.SLDDRW
Solidworks模型/备用/装配体工程图.SLDDRW
Solidworks模型/备用/车轮.SLDPRT
Solidworks模型/备用/车轮工程图.SLDDRW
Solidworks模型/备用/轴1工程图.SLDDRW
Solidworks模型/备用/轴2工程图.SLDDRW
Solidworks模型/备用/连接.SLDPRT
Solidworks模型/备用/连接工程图.SLDDRW
Solidworks模型/备用/零件1 - 副本.SLDDRW
Solidworks模型/备用/零件工程图.SLDDRW
Solidworks模型/投放模块/夹子.SLDPRT
Solidworks模型/投放模块/夹子工程图.SLDDRW
Solidworks模型/投放模块/投放模块装配体工程图.SLDDRW
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

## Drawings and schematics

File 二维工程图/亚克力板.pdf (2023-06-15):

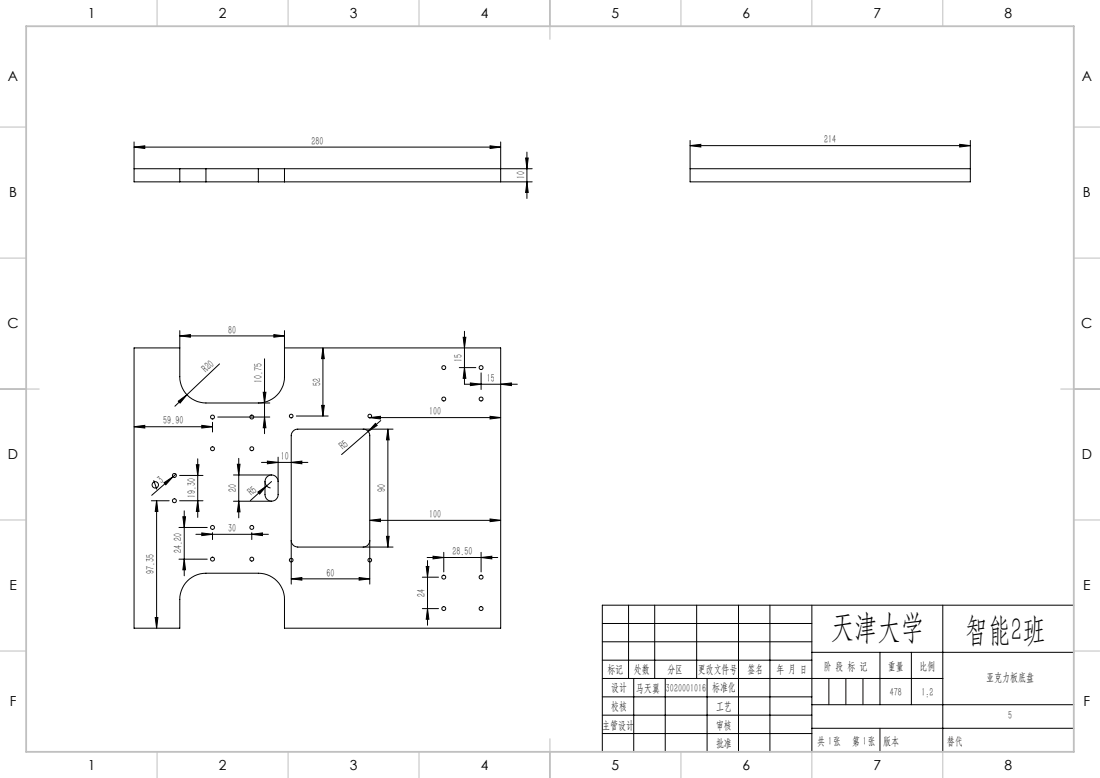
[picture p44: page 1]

天津大学 | 智能2班

阶 段 标 记 | 重量 | 比例 | 亚克力板底盘

标记 | 处数 | 分区 | 更改文件号 | 签名 | 年 月 日
设计 | 马天翼 | 3020001016 | 标准化 | | | 478 | 1:2
校核 | | | 工艺
主管设计 | | | 审核

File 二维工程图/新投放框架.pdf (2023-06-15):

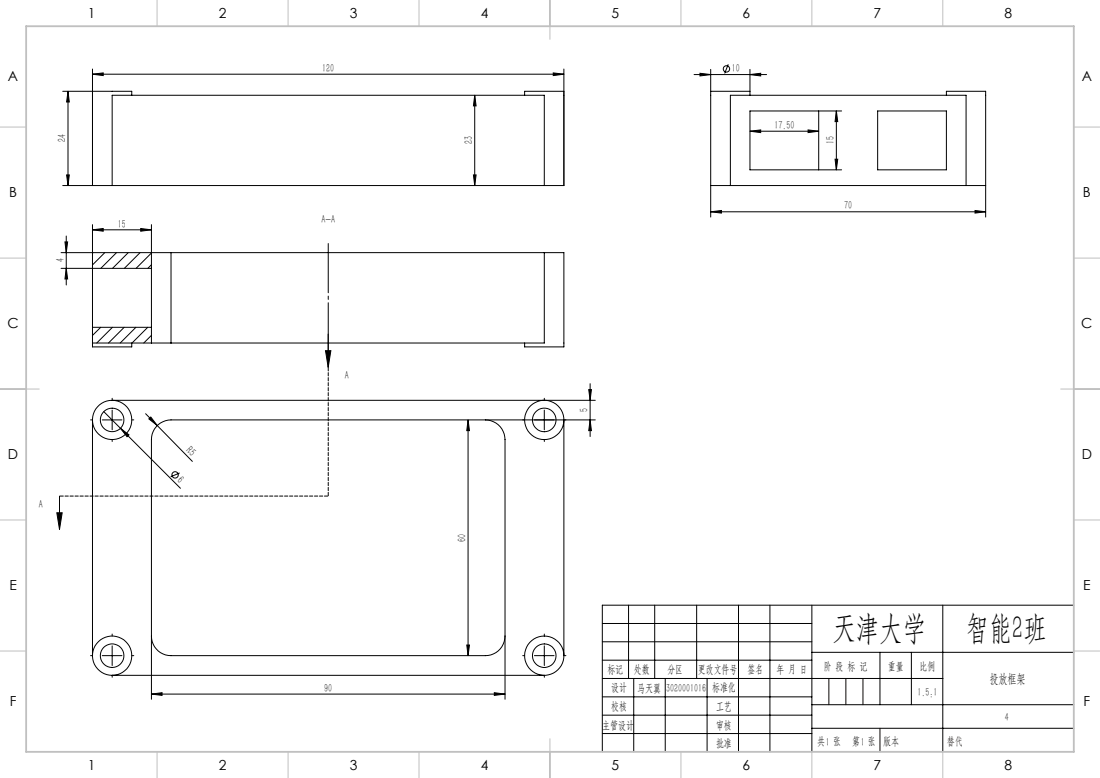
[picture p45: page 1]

天津大学 | 智能2班

阶 段 标 记 | 重量 | 比例 | 投放框架

标记 | 处数 | 分区 | 更改文件号 | 签名 | 年 月 日
设计 | 马天翼 | 3020001016 | 标准化 | | | 1.5:1
校核 | | | 工艺
主管设计 | | | 审核

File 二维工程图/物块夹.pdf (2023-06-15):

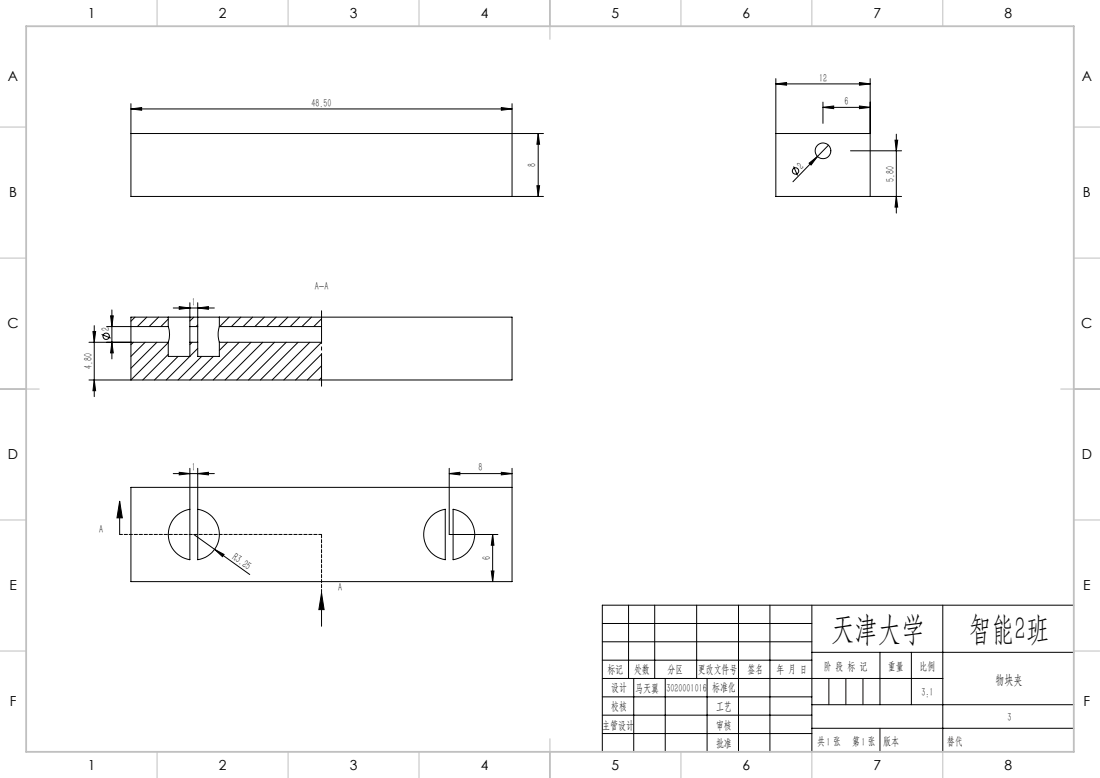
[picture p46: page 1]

天津大学 | 智能2班

阶 段 标 记 | 重量 | 比例 | 物块夹
标记 | 处数 | 分区 | 更改文件号 | 签名 | 年 月 日
设计 | 马天翼 | 3020001016 | 标准化 | | | 3:1

校核 | | | 工艺
主管设计 | | | 审核

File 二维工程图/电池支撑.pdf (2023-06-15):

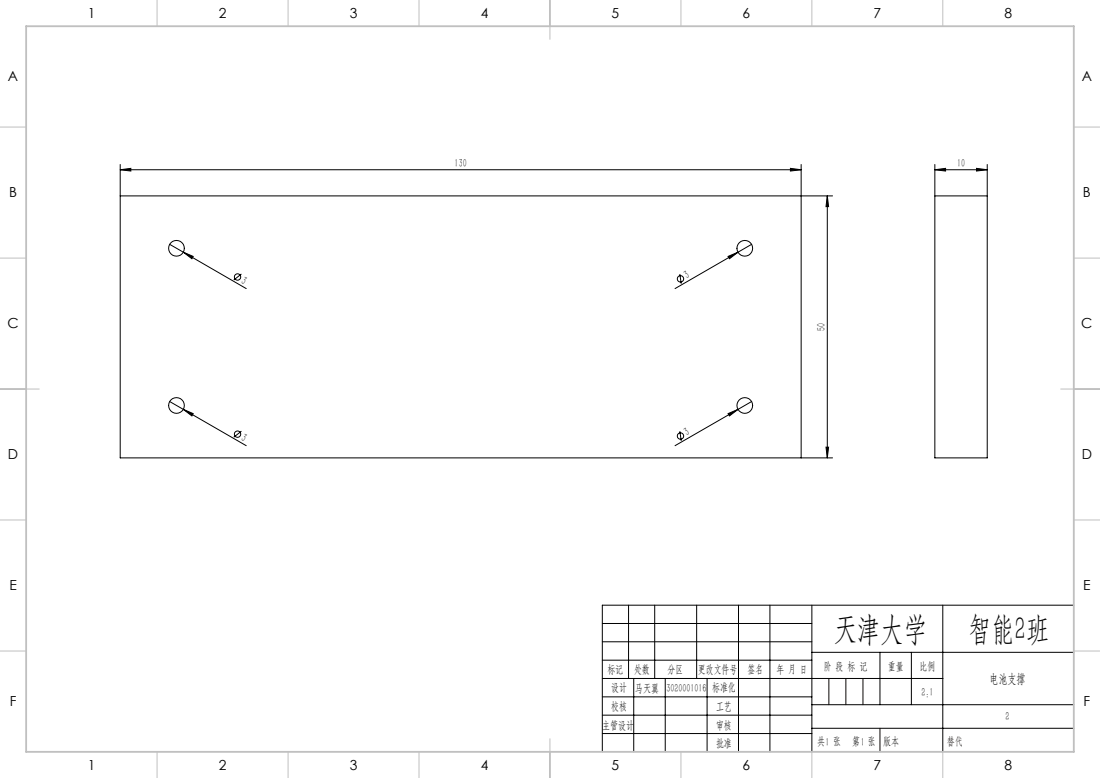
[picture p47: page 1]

天津大学 | 智能2班

阶 段 标 记 | 重量 | 比例 | 电池支撑
标记 | 处数 | 分区 | 更改文件号 | 签名 | 年 月 日
设计 | 马天翼 | 3020001016 | 标准化 | | | 2:1

校核 | | | 工艺
主管设计 | | | 审核

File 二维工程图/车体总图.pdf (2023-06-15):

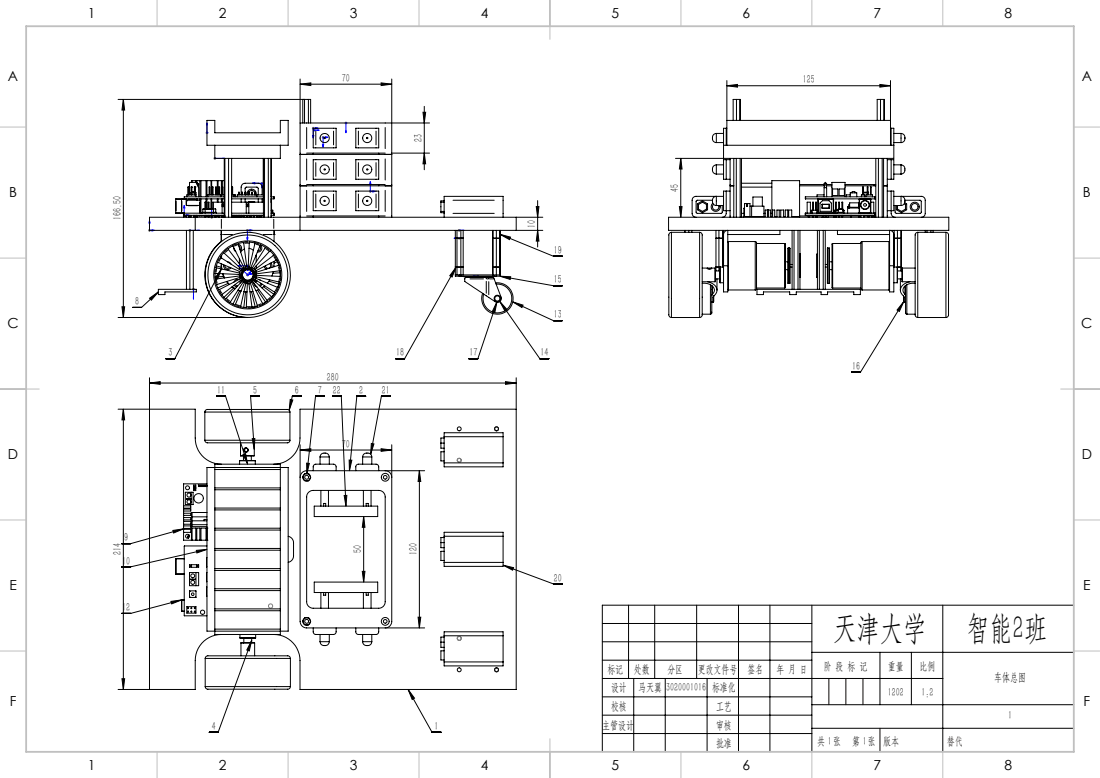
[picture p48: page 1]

天津大学 | 智能2班

阶 段 标 记 | 重量 | 比例 | 车体总图

标记 | 处数 | 分区 | 更改文件号 | 签名 | 年 月 日
设计 | 马天翼 | 3020001016 | 标准化 | | | 1202 | 1:2
校核 | | | 工艺
主管设计 | | | 审核

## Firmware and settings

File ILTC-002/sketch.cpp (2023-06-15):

#include <Arduino.h>

const int sw1 = 8;
const int sw2 = 9;
const int sw3 = 10;
const int sw4 = 11;
//红外传感器端口
const int LMF = 5;
const int LMB = 4;
const int RMF = 3;
const int RMB = 2;
//L298N驱动板端口
const int s1 = 6;
const int s2 = 7;
const int s3 = 12;
//继电器（投放用）
const int s = 13;
//启动键
int m0 = 0;
int m1 = 0;
int m2 = 0;
int m3 = 0;
int m4 = 0;
//投放用变量
int Lv = 180;
int Rv = 180;
//速度
int t1 = 0;
int t2 = 0;
int t3 = 0;

void setup() {
pinMode(sw1,INPUT);
pinMode(sw2,INPUT);
pinMode(sw3,INPUT);
pinMode(sw4,INPUT);
pinMode(LMF,OUTPUT);
pinMode(LMB,OUTPUT);
pinMode(RMF,OUTPUT);
pinMode(RMB,OUTPUT);
pinMode(s1,OUTPUT);
pinMode(s2,OUTPUT);
pinMode(s3,OUTPUT);
pinMode(s,INPUT);


delay(2000);
//延迟1s启动

while(m0 == 0)
{
if(digitalRead(sw2)==1 and digitalRead(sw4)==0)
{
while(digitalRead(sw2)==1 and digitalRead(sw4)==1)
{
digitalWrite(LMF,LOW);
digitalWrite(LMB,HIGH);
digitalWrite(RMF,HIGH);
digitalWrite(RMB,LOW);
}
while(digitalRead(sw2)==1 and digitalRead(sw4)==0)
{
digitalWrite(LMF,LOW);
digitalWrite(LMB,HIGH);
digitalWrite(RMF,HIGH);
digitalWrite(RMB,LOW);
}
}

if(digitalRead(sw2)==0 and digitalRead(sw4)==1)
{
while(digitalRead(sw2)==1 and digitalRead(sw4)==1)
{
digitalWrite(LMF,HIGH);
digitalWrite(LMB,LOW);
digitalWrite(RMF,LOW);
digitalWrite(RMB,HIGH);
}
while(digitalRead(sw2)==0 and digitalRead(sw4)==1)
{
digitalWrite(LMF,HIGH);
digitalWrite(LMB,LOW);
digitalWrite(RMF,LOW);
digitalWrite(RMB,HIGH);
}
}

while(digitalRead(sw2)==1 and digitalRead(sw4)==1)
{
analogWrite(LMF,Lv);
digitalWrite(LMB,LOW);
analogWrite(RMF,Rv);
digitalWrite(RMB,LOW);

}
if(digitalRead(sw2)==0 and digitalRead(sw4)==0)
{
  m0 = 1;

digitalWrite(LMF,HIGH);
digitalWrite(LMB,HIGH);
digitalWrite(RMF,HIGH);
digitalWrite(RMB,HIGH);

while(digitalRead(sw2)==0 or digitalRead(sw4)==0)
{

analogWrite(LMF,Lv);
digitalWrite(LMB,LOW);
analogWrite(RMF,Rv);
digitalWrite(RMB,LOW);
}
}
}
//自动对齐

while(m1 == 0)
{
if(digitalRead(sw2)==1 and digitalRead(sw4)==0)
{
while(digitalRead(sw2)==1 and digitalRead(sw4)==1)
{
digitalWrite(LMF,LOW);
digitalWrite(LMB,HIGH);
digitalWrite(RMF,HIGH);
digitalWrite(RMB,LOW);
}
while(digitalRead(sw3)==1 and digitalRead(sw4)==0)
{
digitalWrite(LMF,LOW);
digitalWrite(LMB,HIGH);
digitalWrite(RMF,HIGH);
digitalWrite(RMB,LOW);
}
}

if(digitalRead(sw2)==0 and digitalRead(sw4)==1)
{
while(digitalRead(sw2)==1 and digitalRead(sw4)==1)
{
digitalWrite(LMF,HIGH);
digitalWrite(LMB,LOW);
digitalWrite(RMF,LOW);
digitalWrite(RMB,HIGH);
}
while(digitalRead(sw2)==0 and digitalRead(sw1)==1)
{
digitalWrite(LMF,HIGH);
digitalWrite(LMB,LOW);
digitalWrite(RMF,LOW);
digitalWrite(RMB,HIGH);
}
}

while(digitalRead(sw2)==1 and digitalRead(sw4)==1)
{
analogWrite(LMF,Lv);
digitalWrite(LMB,LOW);
analogWrite(RMF,Rv);
digitalWrite(RMB,LOW);

}
if(digitalRead(sw2)==0 and digitalRead(sw4)==0)
{
  m1 = 1;

while(digitalRead(sw2)==0 or digitalRead(sw4)==0)
{

analogWrite(LMF,Lv);
digitalWrite(LMB,LOW);
analogWrite(RMF,Rv);
digitalWrite(RMB,LOW);
t1 = t1 + 1;
//delay(1);
}

while(t1 < 4000)
{
  if(digitalRead(sw2)==1 and digitalRead(sw4)==0)
{
while(digitalRead(sw2)==1 and digitalRead(sw4)==1)
{
digitalWrite(LMF,LOW);
digitalWrite(LMB,HIGH);
digitalWrite(RMF,HIGH);
digitalWrite(RMB,LOW);
t1 = t1 + 1;
//delay(1);
}
while(digitalRead(sw3)==1 and digitalRead(sw4)==0)
{
digitalWrite(LMF,LOW);
digitalWrite(LMB,HIGH);
digitalWrite(RMF,HIGH);
digitalWrite(RMB,LOW);
t1 = t1 + 1;
//delay(1);
}
}

if(digitalRead(sw2)==0 and digitalRead(sw4)==1)
{
while(digitalRead(sw2)==1 and digitalRead(sw4)==1)
{
digitalWrite(LMF,HIGH);
digitalWrite(LMB,LOW);
digitalWrite(RMF,LOW);
digitalWrite(RMB,HIGH);
t1 = t1 + 1;
//delay(1);
}
while(digitalRead(sw2)==0 and digitalRead(sw1)==1)
{
digitalWrite(LMF,HIGH);
digitalWrite(LMB,LOW);
digitalWrite(RMF,LOW);
digitalWrite(RMB,HIGH);
t1 = t1 + 1;
//delay(1);
}
}
if(digitalRead(sw2)==1 and digitalRead(sw4)==1)
{
analogWrite(LMF,Lv);
digitalWrite(LMB,LOW);
analogWrite(RMF,Rv);
digitalWrite(RMB,LOW);
t1 = t1 + 1;

}
}

digitalWrite(s1,HIGH);

while(t1 < 7000)
{
  if(digitalRead(sw2)==1 and digitalRead(sw4)==0)
{
while(digitalRead(sw2)==1 and digitalRead(sw4)==1)
{
digitalWrite(LMF,LOW);
digitalWrite(LMB,HIGH);
digitalWrite(RMF,HIGH);
digitalWrite(RMB,LOW);
t1 = t1 + 1;
//delay(1);
}
while(digitalRead(sw3)==1 and digitalRead(sw4)==0)
{
digitalWrite(LMF,LOW);
digitalWrite(LMB,HIGH);
digitalWrite(RMF,HIGH);
digitalWrite(RMB,LOW);
t1 = t1 + 1;
//delay(1);
}
}

if(digitalRead(sw2)==0 and digitalRead(sw4)==1)
{
while(digitalRead(sw2)==1 and digitalRead(sw4)==1)
{
digitalWrite(LMF,HIGH);
digitalWrite(LMB,LOW);
digitalWrite(RMF,LOW);
digitalWrite(RMB,HIGH);
t1 = t1 + 1;
//delay(1);
}
while(digitalRead(sw2)==0 and digitalRead(sw1)==1)
{
digitalWrite(LMF,HIGH);
digitalWrite(LMB,LOW);
digitalWrite(RMF,LOW);
digitalWrite(RMB,HIGH);
t1 = t1 + 1;
//delay(1);
}
}
if(digitalRead(sw2)==1 and digitalRead(sw4)==1)
{
analogWrite(LMF,Lv);
digitalWrite(LMB,LOW);
analogWrite(RMF,Rv);
digitalWrite(RMB,LOW);
t1 = t1 + 1;

}
}
digitalWrite(s1,LOW);
}
}
//---------------------------------------------------1--------------------------------------------------
while(m2 == 0)
{
if(digitalRead(sw2)==1 and digitalRead(sw4)==0)
{
while(digitalRead(sw2)==1 and digitalRead(sw4)==1)
{
digitalWrite(LMF,LOW);
digitalWrite(LMB,HIGH);
digitalWrite(RMF,HIGH);
digitalWrite(RMB,LOW);
}
while(digitalRead(sw3)==1 and digitalRead(sw4)==0)
{
digitalWrite(LMF,LOW);
digitalWrite(LMB,HIGH);
digitalWrite(RMF,HIGH);
digitalWrite(RMB,LOW);
}
}

if(digitalRead(sw2)==0 and digitalRead(sw4)==1)
{
while(digitalRead(sw2)==1 and digitalRead(sw4)==1)
{
digitalWrite(LMF,HIGH);
digitalWrite(LMB,LOW);
digitalWrite(RMF,LOW);
digitalWrite(RMB,HIGH);
}
while(digitalRead(sw2)==0 and digitalRead(sw1)==1)
{
digitalWrite(LMF,HIGH);
digitalWrite(LMB,LOW);
digitalWrite(RMF,LOW);
digitalWrite(RMB,HIGH);
}
}

while(digitalRead(sw2)==1 and digitalRead(sw4)==1)
{
analogWrite(LMF,Lv);
digitalWrite(LMB,LOW);
analogWrite(RMF,Rv);
digitalWrite(RMB,LOW);

}
if(digitalRead(sw2)==0 and digitalRead(sw4)==0)
{
  m2 = 1;

while(digitalRead(sw2)==0 or digitalRead(sw4)==0)
{

analogWrite(LMF,Lv);
digitalWrite(LMB,LOW);
analogWrite(RMF,Rv);
digitalWrite(RMB,LOW);
t2 = t2 + 1;
//delay(1);
}

while(t2 < 4000)
{
  if(digitalRead(sw2)==1 and digitalRead(sw4)==0)
{
while(digitalRead(sw2)==1 and digitalRead(sw4)==1)
{
digitalWrite(LMF,LOW);
digitalWrite(LMB,HIGH);
digitalWrite(RMF,HIGH);
digitalWrite(RMB,LOW);
t2 = t2 + 1;
//delay(1);
}
while(digitalRead(sw3)==1 and digitalRead(sw4)==0)
{
digitalWrite(LMF,LOW);
digitalWrite(LMB,HIGH);
digitalWrite(RMF,HIGH);
digitalWrite(RMB,LOW);
t2 = t2 + 1;
//delay(1);
}
}

if(digitalRead(sw2)==0 and digitalRead(sw4)==1)
{
while(digitalRead(sw2)==1 and digitalRead(sw4)==1)
{
digitalWrite(LMF,HIGH);
digitalWrite(LMB,LOW);
digitalWrite(RMF,LOW);
digitalWrite(RMB,HIGH);
t2 = t2 + 1;
//delay(1);
}
while(digitalRead(sw2)==0 and digitalRead(sw1)==1)
{
digitalWrite(LMF,HIGH);
digitalWrite(LMB,LOW);
digitalWrite(RMF,LOW);
digitalWrite(RMB,HIGH);
t2 = t2 + 1;
//delay(1);
}
}
if(digitalRead(sw2)==1 and digitalRead(sw4)==1)
{
analogWrite(LMF,Lv);
digitalWrite(LMB,LOW);
analogWrite(RMF,Rv);
digitalWrite(RMB,LOW);
t2 = t2 + 1;

}
}

digitalWrite(s1,HIGH);
digitalWrite(s2,HIGH);

while(t2 < 7000)
{
  if(digitalRead(sw2)==1 and digitalRead(sw4)==0)
{
while(digitalRead(sw2)==1 and digitalRead(sw4)==1)
{
digitalWrite(LMF,LOW);
digitalWrite(LMB,HIGH);
digitalWrite(RMF,HIGH);
digitalWrite(RMB,LOW);
t2 = t2 + 1;
//delay(1);
}
while(digitalRead(sw3)==1 and digitalRead(sw4)==0)
{
digitalWrite(LMF,LOW);
digitalWrite(LMB,HIGH);
digitalWrite(RMF,HIGH);
digitalWrite(RMB,LOW);
t2 = t2 + 1;
//delay(1);
}
}

if(digitalRead(sw2)==0 and digitalRead(sw4)==1)
{
while(digitalRead(sw2)==1 and digitalRead(sw4)==1)
{
digitalWrite(LMF,HIGH);
digitalWrite(LMB,LOW);
digitalWrite(RMF,LOW);
digitalWrite(RMB,HIGH);
t2 = t2 + 1;
//delay(1);
}
while(digitalRead(sw2)==0 and digitalRead(sw1)==1)
{
digitalWrite(LMF,HIGH);
digitalWrite(LMB,LOW);
digitalWrite(RMF,LOW);
digitalWrite(RMB,HIGH);
t2 = t2 + 1;
//delay(1);
}
}
if(digitalRead(sw2)==1 and digitalRead(sw4)==1)
{
analogWrite(LMF,Lv);
digitalWrite(LMB,LOW);
analogWrite(RMF,Rv);
digitalWrite(RMB,LOW);
t2 = t2 + 1;

}
}
digitalWrite(s1,LOW);
digitalWrite(s2,LOW);
}
}
//---------------------------------------------------2--------------------------------------------------
while(m3 == 0)
{
if(digitalRead(sw2)==1 and digitalRead(sw4)==0)
{
while(digitalRead(sw2)==1 and digitalRead(sw4)==1)
{
digitalWrite(LMF,LOW);
digitalWrite(LMB,HIGH);
digitalWrite(RMF,HIGH);
digitalWrite(RMB,LOW);
}
while(digitalRead(sw3)==1 and digitalRead(sw4)==0)
{
digitalWrite(LMF,LOW);
digitalWrite(LMB,HIGH);
digitalWrite(RMF,HIGH);
digitalWrite(RMB,LOW);
}
}

if(digitalRead(sw2)==0 and digitalRead(sw4)==1)
{
while(digitalRead(sw2)==1 and digitalRead(sw4)==1)
{
digitalWrite(LMF,HIGH);
digitalWrite(LMB,LOW);
digitalWrite(RMF,LOW);
digitalWrite(RMB,HIGH);
}
while(digitalRead(sw2)==0 and digitalRead(sw1)==1)
{
digitalWrite(LMF,HIGH);
digitalWrite(LMB,LOW);
digitalWrite(RMF,LOW);
digitalWrite(RMB,HIGH);
}
}

while(digitalRead(sw2)==1 and digitalRead(sw4)==1)
{
analogWrite(LMF,Lv);
digitalWrite(LMB,LOW);
analogWrite(RMF,Rv);
digitalWrite(RMB,LOW);

}
if(digitalRead(sw2)==0 and digitalRead(sw4)==0)
{
  m3 = 1;

while(digitalRead(sw2)==0 or digitalRead(sw4)==0)
{

analogWrite(LMF,Lv);
digitalWrite(LMB,LOW);
analogWrite(RMF,Rv);
digitalWrite(RMB,LOW);
t3 = t3 + 1;
//delay(1);
}

while(t3 < 4000)
{
  if(digitalRead(sw2)==1 and digitalRead(sw4)==0)
{
while(digitalRead(sw2)==1 and digitalRead(sw4)==1)
{
digitalWrite(LMF,LOW);
digitalWrite(LMB,HIGH);
digitalWrite(RMF,HIGH);
digitalWrite(RMB,LOW);
t3 = t3 + 1;
//delay(1);
}
while(digitalRead(sw3)==1 and digitalRead(sw4)==0)
{
digitalWrite(LMF,LOW);
digitalWrite(LMB,HIGH);
digitalWrite(RMF,HIGH);
digitalWrite(RMB,LOW);
t3 = t3 + 1;
//delay(1);
}
}

if(digitalRead(sw2)==0 and digitalRead(sw4)==1)
{
while(digitalRead(sw2)==1 and digitalRead(sw4)==1)
{
digitalWrite(LMF,HIGH);
digitalWrite(LMB,LOW);
digitalWrite(RMF,LOW);
digitalWrite(RMB,HIGH);
t3 = t3 + 1;
//delay(1);
}
while(digitalRead(sw2)==0 and digitalRead(sw1)==1)
{
digitalWrite(LMF,HIGH);
digitalWrite(LMB,LOW);
digitalWrite(RMF,LOW);
digitalWrite(RMB,HIGH);
t3 = t3 + 1;
//delay(1);
}
}
if(digitalRead(sw2)==1 and digitalRead(sw4)==1)
{
analogWrite(LMF,Lv);
digitalWrite(LMB,LOW);
analogWrite(RMF,Rv);
digitalWrite(RMB,LOW);
t3 = t3 + 1;

}
}

digitalWrite(s1,HIGH);
digitalWrite(s2,HIGH);
digitalWrite(s3,HIGH);
while(t3 < 8000)
{
  if(digitalRead(sw2)==1 and digitalRead(sw4)==0)
{
while(digitalRead(sw2)==1 and digitalRead(sw4)==1)
{
digitalWrite(LMF,LOW);
digitalWrite(LMB,HIGH);
digitalWrite(RMF,HIGH);
digitalWrite(RMB,LOW);
t3 = t3 + 1;
//delay(1);
}
while(digitalRead(sw3)==1 and digitalRead(sw4)==0)
{
digitalWrite(LMF,LOW);
digitalWrite(LMB,HIGH);
digitalWrite(RMF,HIGH);
digitalWrite(RMB,LOW);
t3 = t3 + 1;
//delay(1);
}
}

if(digitalRead(sw2)==0 and digitalRead(sw4)==1)
{
while(digitalRead(sw2)==1 and digitalRead(sw4)==1)
{
digitalWrite(LMF,HIGH);
digitalWrite(LMB,LOW);
digitalWrite(RMF,LOW);
digitalWrite(RMB,HIGH);
t3 = t3 + 1;
//delay(1);
}
while(digitalRead(sw2)==0 and digitalRead(sw1)==1)
{
digitalWrite(LMF,HIGH);
digitalWrite(LMB,LOW);
digitalWrite(RMF,LOW);
digitalWrite(RMB,HIGH);
t3 = t3 + 1;
//delay(1);
}
}
if(digitalRead(sw2)==1 and digitalRead(sw4)==1)
{
analogWrite(LMF,Lv);
digitalWrite(LMB,LOW);
analogWrite(RMF,Rv);
digitalWrite(RMB,LOW);
t3 = t3 + 1;

}
}
digitalWrite(s1,LOW);
digitalWrite(s2,LOW);
digitalWrite(s3,LOW);

}
}
//---------------------------------------------------3--------------------------------------------------
while(m4 == 0)
{
if(digitalRead(sw2)==1 and digitalRead(sw4)==0)
{
while(digitalRead(sw2)==1 and digitalRead(sw4)==1)
{
digitalWrite(LMF,LOW);
digitalWrite(LMB,HIGH);
digitalWrite(RMF,HIGH);
digitalWrite(RMB,LOW);
}
while(digitalRead(sw2)==1 and digitalRead(sw4)==0)
{
digitalWrite(LMF,LOW);
digitalWrite(LMB,HIGH);
analogWrite(RMF,255);
digitalWrite(RMB,LOW);
}
}

if(digitalRead(sw2)==0 and digitalRead(sw4)==1)
{
while(digitalRead(sw2)==1 and digitalRead(sw4)==1)
{
digitalWrite(LMF,HIGH);
digitalWrite(LMB,LOW);
digitalWrite(RMF,LOW);
digitalWrite(RMB,HIGH);
}
while(digitalRead(sw2)==0 and digitalRead(sw4)==1)
{
analogWrite(LMF,255);
digitalWrite(LMB,LOW);
digitalWrite(RMF,LOW);
digitalWrite(RMB,HIGH);
}
}

while(digitalRead(sw2)==1 and digitalRead(sw4)==1)
{
analogWrite(LMF,150);
digitalWrite(LMB,LOW);
analogWrite(RMF,150);
digitalWrite(RMB,LOW);

}
if(digitalRead(sw2)==0 and digitalRead(sw4)==0)
{
  m4 = 1;

digitalWrite(LMF,LOW);
digitalWrite(LMB,LOW);
digitalWrite(RMF,LOW);
digitalWrite(RMB,LOW);


}
}

}
void loop() {


}
